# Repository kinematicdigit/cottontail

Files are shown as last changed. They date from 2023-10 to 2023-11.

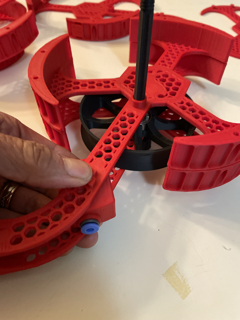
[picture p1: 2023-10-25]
IMG/IMG_6659 Small.png

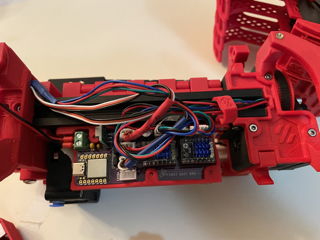
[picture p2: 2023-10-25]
IMG/IMG_6661 Small.png

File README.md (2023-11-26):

##Cotton Tail for ERCF

## BETA IS CURRENTLY CLOSED UNTIL RELEASE - TBA!

**This is project is still underdevelopment, **please proceed with caution. I hold no responsibilities for any personal damages for the use of any of these files. Please do not modifiy or share any of the files.

Any bugs, observations, questions related to this buffer can be directed at my home server at <https://discord.gg/Gs2vAtK7T7>

@kinematicdigit



Cotton Tail buffer system will attach directly to the Sturdy Bunny upgraded ERCF and is designed to work with any number of filament blocks you choose (the initial test phase will go up to 9). 

The primary goal of this project was to reduce as much resistance in the path and to remove any inconsistencies in calibration. It works with Triple Decky but will work with whatever top hat/filament block design you want. In fact, there is no limitation to the design, and it also may remove the need for magnets in them altogether. There is a spring in the couplers to alleviate all pressure on the magnets.

This system is also designed to reduce the buffer length, which will help reduce friction on the entire system. There will also be optional QoL features to work with the new BTT MMB Can board.
Features:
- Large central buffer wheel - reduces the filament's natural shape - each wheel comes pre-notched to make loading filament easier.
- Inline connection - connects to the 2020 extrusion arm
- Short Buffer Length - Can operate as low as 500mm in buffer Length
- Reduced resistance - Tests up to 200 mm/s (with Galileo 2 extruder) - may do less or more depending on your extruder motor
- Improved encoder accuracy - makes all resistance more consistent for better encoder performance and less torque needed
- Stackable Arm - Each arm is stackable for whatever combination of gates you want. They are optimized for strength and weight and provide access for loading and unloading filament
- Uses most parts from ERCP -  if you already have a kit, most parts should be interchangeable.
- Filament Detector - Each coupler has a filament detector built in. This is optional and will interface with the new BTT MMB Can board. 
- Filament indicator - Future QoL option that will include the ability to light up each gate to tell you if it is loaded/active and empty/out of filament.

###

***

### BOM (Each arm group/channel):

* (8) 8mm M3 screws
* (1) 16mm M3 screw
* (1) 25mm M3 screw
* (1) M3 threaded inserts (M3x5x4mm) Heat Sets
* PTFE Tubing (4mm OD/3MM ID recommended)
* (1) 608 ZZ Bearing (same as ERCP - skateboard bearings will work as well)
* (1) ECAS
* (2) M3 Hammerhead T-Nuts (for attaching to 2020 extrusions)

### End cap (with integrated MMB CASE) needs:

* (6) 8mm M3 screws
* (5) 25mm M3 screw (1) for non MMB
* (4) M3 threaded inserts (M3x5x4mm) Heat Sets (0) for non MMB

**The optional MMB version build requires:**

(1) BTT MMB Can board
(1) Microswitch per arm
(1) 5.5 mm ball bearing per arm
(2) 12mm M2 BHCS screws per arm
(1) Button Neopixels per arm

***

## Building the ERCT

All files are located in the STL folder, and instructions are as follows:

|  |
| :-----------------------------------------------------------------------------------------------------------------------------------------------------------------------------------------------------------------------------------------------------------------------------------: |
|                                                                                            Each channel uses these parts. ERCT is all stackable with a single endcap to finish the buffer.                                                                                            |

### **Instructions**

**PRINT SETTINGS**

.25mm first layer, .2mm Layer Height
4 Perimeters (top, bottom, walls

Arms should be printed at .2 layer height, with 4 walls and 10% lightning infill. This will significantly reduce the amount of filament used. ABS is the recommended material or PETG.

Wheels should be printed on a smooth plate, or if you use a textured plate you may need to run it on some sandpaper afterwards to avoid too much contact with the arm. There will always be a small chance of some rubbing, but with careful pressure on the hubs when installing, you shouldn't have any major resistance.

The rest of the parts can be printed with 20-30% gyroid infill.

|   | Start with your printed channel arm and add a 4 mm-deep M3 heatset installed into the back of the arm. Be careful not to go too far past the dovetail channel- it's better to be shy than to go over. |
| ---: | --- |
|   | Print the correct length axial screw. The files are labelled for how many channels. They are longer than needed in case you need to put a bypass divider or extra support. Use the matching nut and work it through the acme screw to make it smooth. A brass brush can also be used to clean it up a little. It is recommended if you make more than 9 channels, to self-source a trapezoidal bar screw (also known as ACME screw). T8, Pitch 2 is a common one. You can also use a traditional screw. Make sure to get matching nuts to add to each end for those builds. |
|   | Load the axial through the first arm. |
|  | The 608 bearings should slide in with just a tiny bit of resistance. |
|   | Make sure the filament loading holes are as pictured, and load the axial from the flat side of the wheel. |
|   | When pushing down on the axial, put your thumbs on each side of the bearing and push down with moderate force. Don't push too hard. If it doesn't go on, use a little sandpaper on the axial to reduce it. It is a tight fit but should slide on. Your pressure on the bearings will ensure the wheel is as balanced as possible. There's a very tiny bit of gap between the wheel and the side of the arm. Don't worry too much if it isn't perfect, but you can try to balance it and spin it to check. |
|  | Preload the M3 Hammerhead T-Nuts onto the mounting bracket. Don't screw in too tight as you need to turn the nuts easily to load into the v-slots of the 2020 extrusion. |
|  | Load the mount onto the arm. The dovetail is snug but should slide on with some pressure. Once seated add the M3 16mm screw to secure it. |
|  | Squeeze the printed spring (the spring goes towards the ECAS side) and slide into the slot on the sloped side.&#xA; |
|  | Add ECAS fitting in the hole. It should snap-in and firm press.&#xA; |
|  | line up the coupler as pictured to the three receiving pins. It should press fit with a small bit of resistance. Repeat the next channel arm until all is loaded. |
|  | When you reach the final channel, you will add the end cap and install the final M3 25mm screw. |
|  | Secure all 6 screws, which enter at an angle. They self-tap into the plastic, so don't over-tighten or you'll strip the plastic. These install and reinstall multiple times if you don't over-tighten.  &#xA; |
|  | The next step is prepping the ERCF. If you have wiring clips, remove them and free all your wires. |
|  | Line up the t-nuts as best you can. Make sure you didn't wind them all the way down. The screws should have enough friction to hold them in place to make this part easier for you. It should sit right on the shoulder and slip in. If not, jiggle the arms a little; it should all mate perfectly. Grab your driver and turn, and it should tighten right away. If not, back off a quick half-turn and turn the back the other way to load the nut in place. |
|   | The last set of steps starts by cutting around 85mm of tube which should leave around 10mm of tube sticking out of the coupler block. |
|  | Insert the cut PTFE tube from the rear of the assembly. Push lightly in the spring, and it should feed through. |
|  | Line up to the channel and press into the ECAS on the filament block. |
|  | The rest of the tube can be trimmed to around 10mm. |
|  | The wires can now be routed against the mounting brackets and you can use zip ties to secure it. |

***

**LOADING THE BUFFER**

|  | To load the buffer, filament from your reverse Bowden. Try your best to work with the natural curl of the filament and feed it till you see it pop out on top. |
| ---: | :--- |
|  | Grab it from up top, and curl it back into one of the multiple filament loading holes located along one side of the buffer wheel. |
|  | Turn the wheel until you have the number of rows needed for your tube length between the ERCF encoder and the tool head (to calculate the right length, measure the tube and divide by 230mm. This will equal the number of rows you need to wrap around the wheel - maximum of 7). |
|  | Back below, grab the filament on the wheel and pull it out. |
|  | Give yourself some length (about 30 cm). |
|  | Feed back into the tube located there. |
|  | It will feed through, and you should feel some resistance from the trap; press on the top hat to help it through. |
|  | The final step is to push the filament flush to the opening so it doesn’t catch on the selector. That’s it. Load it all up, and away you go! |

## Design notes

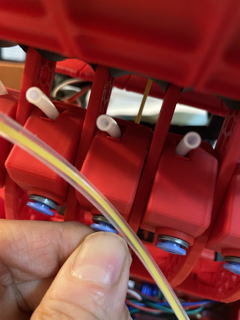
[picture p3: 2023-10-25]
IMG/IMG_6672 Small.png

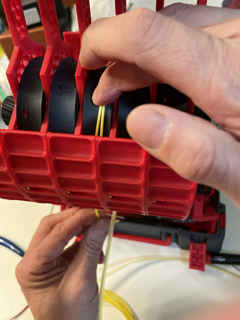
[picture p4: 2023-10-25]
IMG/IMG_6676 Small.png

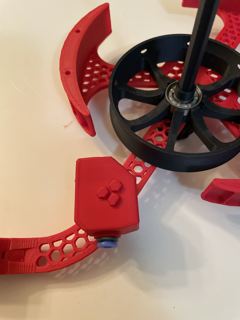
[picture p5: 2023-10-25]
IMG/IMG_6658 Small.png

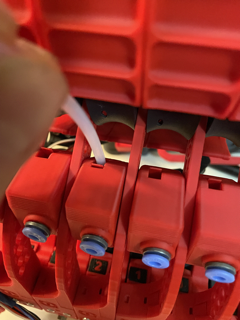
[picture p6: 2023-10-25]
IMG/IMG_6666 Small.png

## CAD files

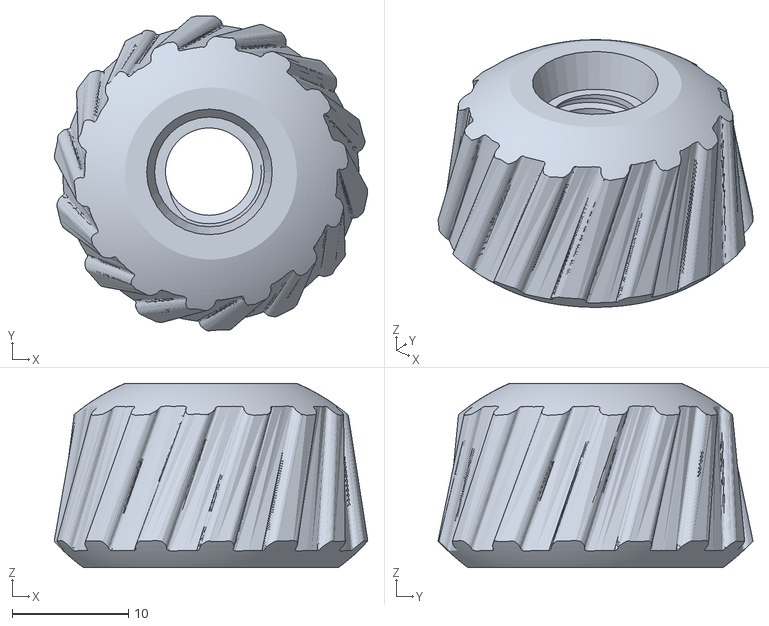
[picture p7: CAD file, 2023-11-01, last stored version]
STLS/[a]knut.stl
27.0 x 27.1 x 15.9

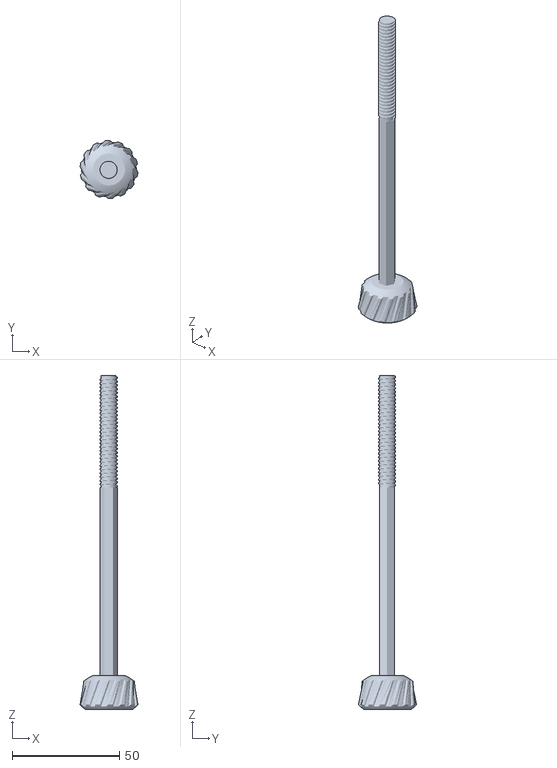
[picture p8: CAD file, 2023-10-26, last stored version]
STLS/axials/[a]kaxial_5.stl
27.0 x 27.1 x 155.6

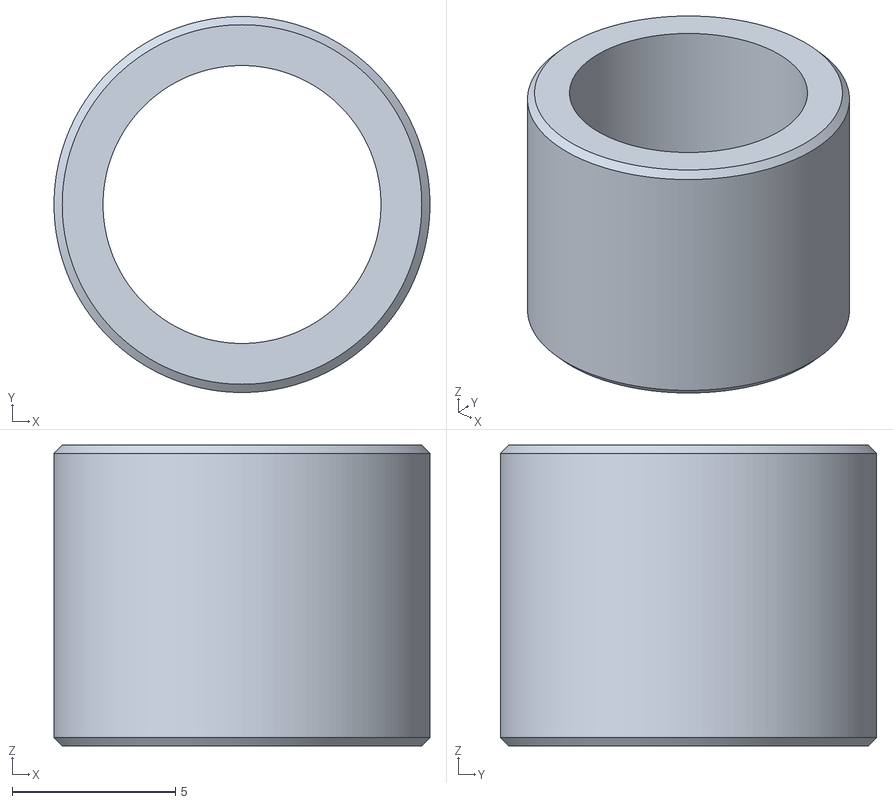
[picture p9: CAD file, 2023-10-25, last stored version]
STLS/buffer_wheel/spacer_bypass.stl
11.5 x 11.5 x 9.20

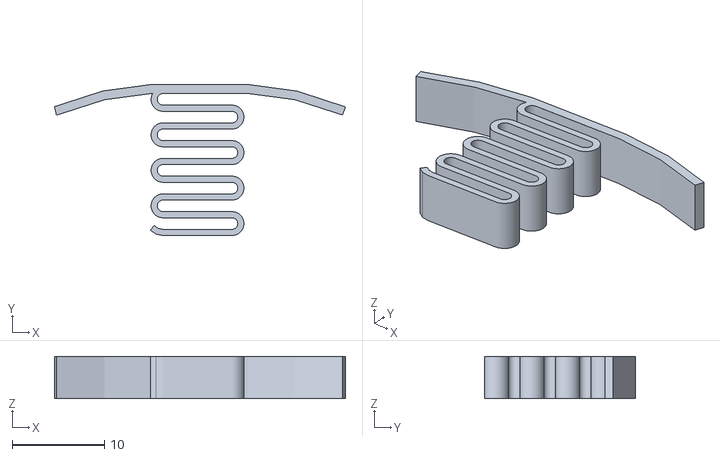
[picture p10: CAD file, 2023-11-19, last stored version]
STLS/coupler/coupler_spring.stl
31.6 x 16.4 x 4.59

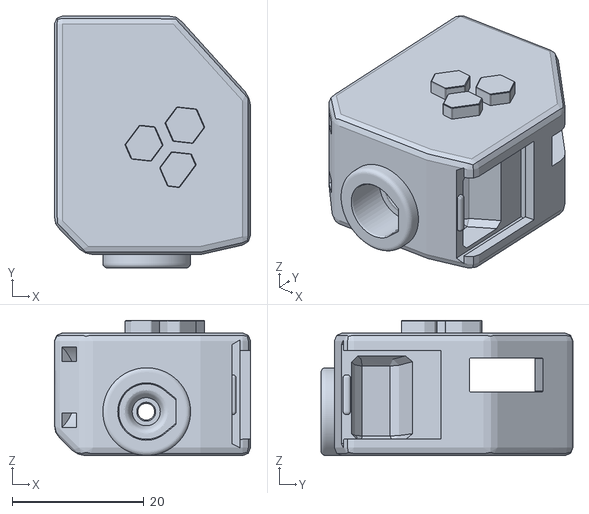
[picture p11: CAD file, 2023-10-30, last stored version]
STLS/coupler/MMB_option/[t]coupler_block_MMB.stl
29.7 x 38.2 x 20.5

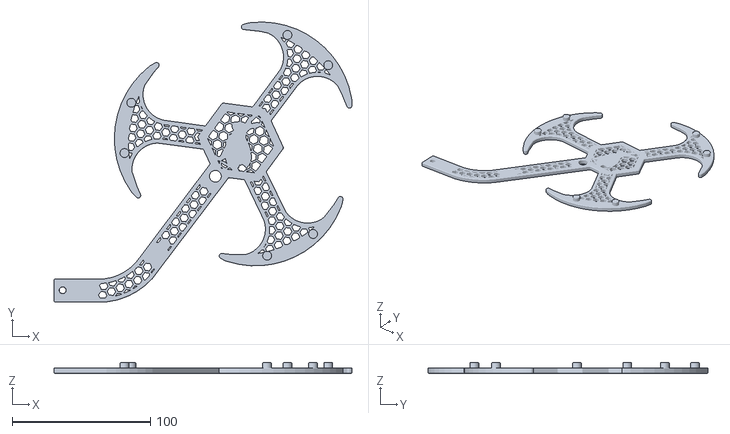
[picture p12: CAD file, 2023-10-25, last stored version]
STLS/support_arms/support_arm_endcap.stl
215.7 x 202.6 x 7.67

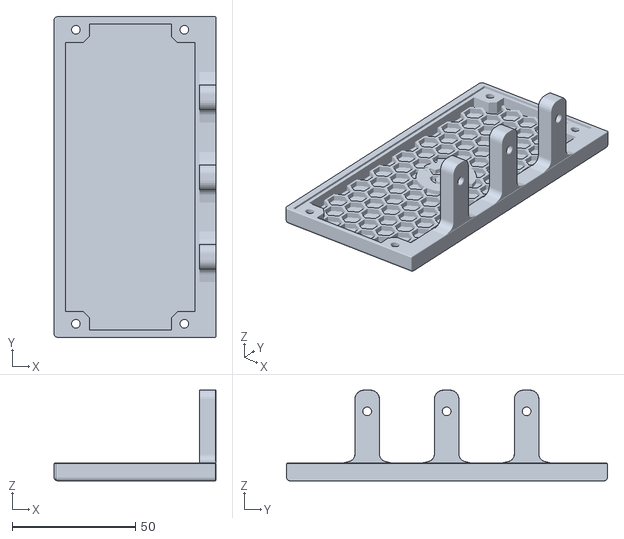
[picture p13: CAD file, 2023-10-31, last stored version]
STLS/supports/BTT_MMB/[a]BTT_MMB_Bottom_Bracket.stl
65.6 x 130.0 x 36.8

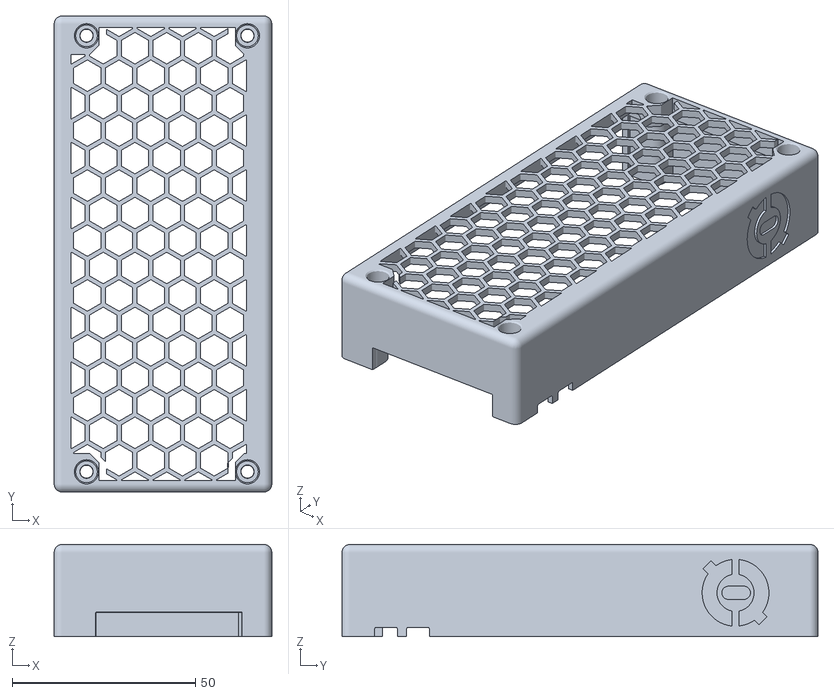
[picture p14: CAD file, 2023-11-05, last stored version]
STLS/supports/BTT_MMB/bottommount/[a]BTT_MMB_Top_Lid_Standard.stl
59.4 x 130.0 x 25.1

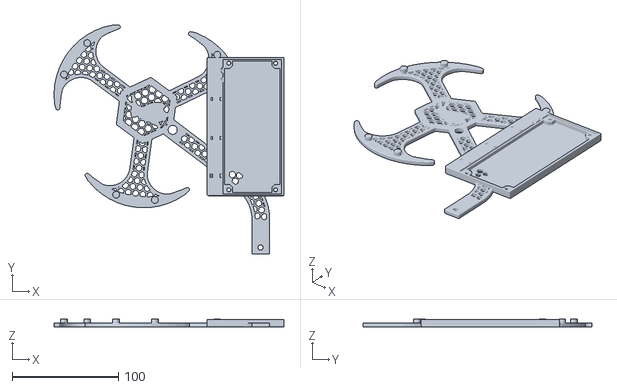
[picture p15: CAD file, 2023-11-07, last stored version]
STLS/supports/BTT_MMB/buffermount_recommended/[a]BTT_MMB_Bottom_Bracket_universal.stl
216.2 x 215.7 x 7.67

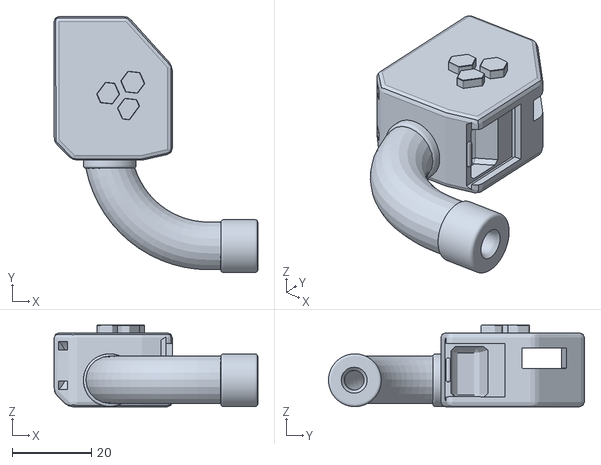
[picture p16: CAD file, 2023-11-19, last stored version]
STLS/testing_experimental/coupler_block_180.stl
51.3 x 64.4 x 20.5

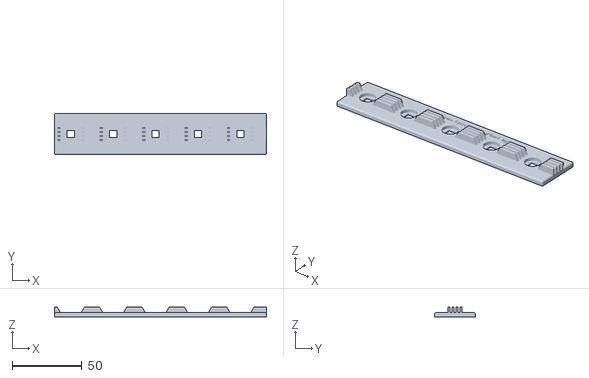
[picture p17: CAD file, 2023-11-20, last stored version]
STLS/tools/LED_Soldering_tool_holder_by_jose.stl
152.5 x 29.5 x 7.00

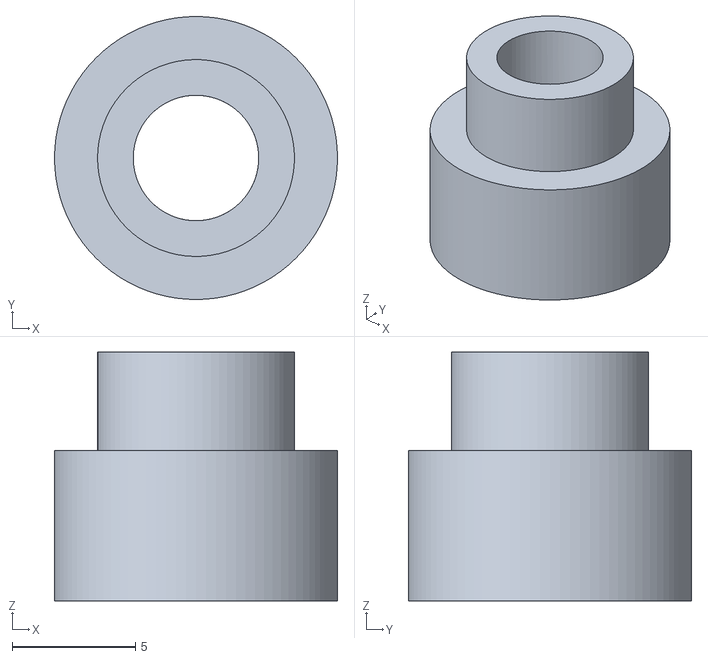
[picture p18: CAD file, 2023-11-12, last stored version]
usermod/Wolffy01/625 mod w 5mm tread rod/stl/5mm arm end cap bushing.stl
11.5 x 11.5 x 10.1

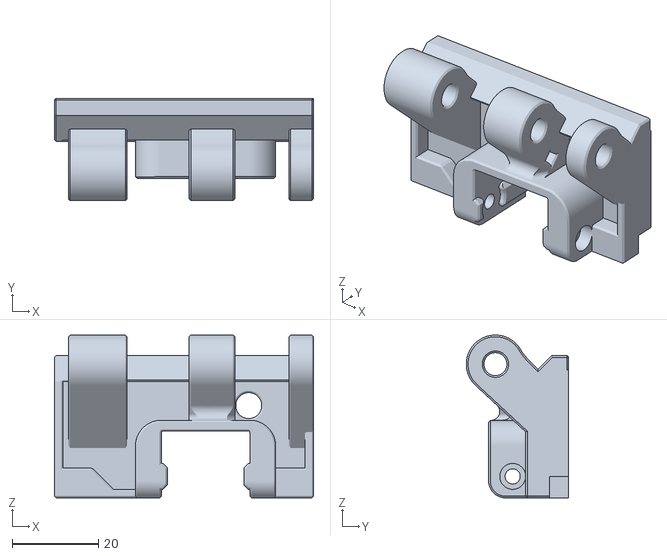
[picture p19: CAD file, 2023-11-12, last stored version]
usermod/Wolffy01/filament_block_end/Filament_Blocks_End_Nobearing_V2C.stl
60.0 x 23.7 x 37.7

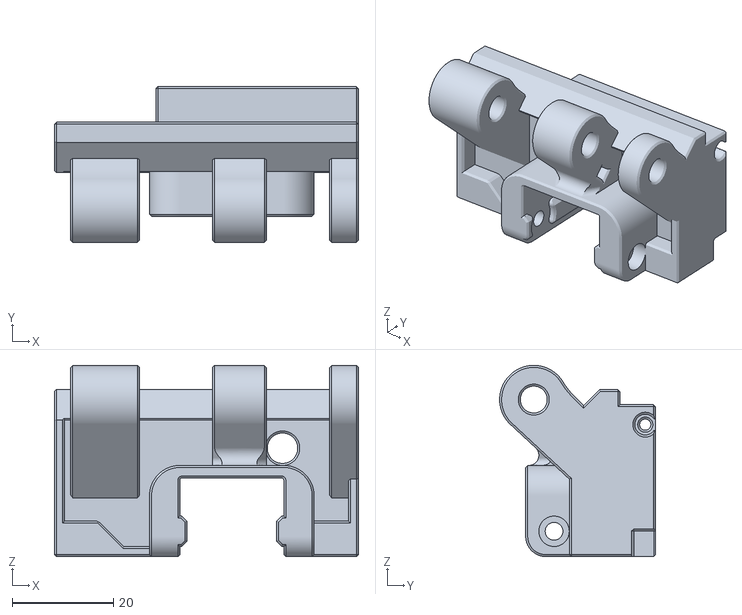
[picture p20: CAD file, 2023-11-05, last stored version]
usermod/wolffy01_filament_block_end/Filament_Blocks_End_Nobearing_V2B.stl
60.0 x 30.8 x 37.7

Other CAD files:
STLS/buffer_wheel/spacer_standard.stl
STLS/coupler/MMB_option/[black]LED_carrier.stl
STLS/axials/[a]axial_spacer.stl
STLS/axials/[a]kaxial_6.stl
STLS/axials/[a]kaxial_7.stl
STLS/axials/[a]kaxial_8.stl
STLS/axials/[a]kaxial_9.stl
STLS/axials/[a]knut.stl
STLS/buffer_wheel/[a]buffer_wheel.stl
STLS/coupler/LED_carrier.stl
STLS/coupler/[a]coupler_block_standard.stl
STLS/coupler/[b]coupler_spring.stl
STLS/coupler/[b]coupler_spring_thicker.stl
STLS/coupler/[black]LED_carrier.stl
STLS/coupler/coupler_spring_thicker.stl
STLS/support_arms/[a]support_arm_mount.stl
STLS/supports/BTT_MMB/bottommount/[a]BTT_MMB_Bottom_Bracket.stl
STLS/supports/BTT_MMB/bottommount/[a]BTT_MMB_Top_Lid_180.stl
STLS/supports/BTT_MMB/buffermount_recommended/[a]support_arm_endcap_case.stl
STLS/supports/BTT_MMB/buffermount_recommended/support_arm_endcap_case.stl
STLS/testing_experimental/[a]arm_anchor_ptfe.stl
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

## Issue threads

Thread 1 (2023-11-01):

soldering tool orientation

99dreada, 2023-11-01:
soldering tool orientation by default is not in a printable way

easy fix but would be nice to be done by default

99dreada, 2023-11-01:
to add to this the Knut is also upside down

kinematicdigit, 2023-11-01:
Thanks for that... reoriented.

Closed 2023-11-01.

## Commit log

2023-10-25 Initial commit
    Update [a]support_arm_mount.stl
    bevelled tip of dovetail
    Adjust Tolerances
    October 23 Late update
    Add files via upload
    Create .gitignore
    Update Oct 23
    New Uploads
    New Uploads
    Create support_arm_00.stl
    [LED_Soldering_tool_holder.stl, LED_carrier.stl, [a]axial_spacer.stl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]
2023-10-25 renaming and reorganizng
    [[a]axial_spacer_bypass.stl, spacer_standard.stl]
2023-10-26 No number plate arm.
2023-10-26 Replace Corrupted File
    [[a]kaxial_5.stl]
2023-10-27 number plate holder update
    Use the same plates found in the Triple Decky repo
2023-10-27 renamed, blank and number plate holder
2023-10-28 Thicker spring for slicers that are having issues with 6mm ones.
    Optional thicker version. This is strictly for slicers that are having issues with the .6mm thick spring. This one is .7mm thick.
    [[b]coupler_spring_thicker.stl]
2023-10-28 ECAS update - now snap fit instead of just a press fit.
    Updated coupler to be snap in fit instead of just a pressure fit. Utilizes a 8.6mm step inside to hold the coupler in place better. Old version will work, but this just makes it a little more secure.
    Thanks to @danzaywer for bringing this to my attention.
    [[a]coupler_block_standard.stl, [t]coupler_block_MMB.stl]
2023-10-30 Coupler Block for BTT MBB versions
    Updated filament path and optimized micro switch operations.
    [[t]coupler_block_MMB.stl]
2023-10-31 BTT_MMB Bracket
    for 2020 extrusion (ERCF - Sturdy Bunny)
    [[a]BTT_MMB_Bottom_Bracket.stl]
2023-11-01 Reoriented for optimal print positions
    [[a]knut.stl]
2023-11-05 Case updates got BTT MBB
    Several Case options for the BTT MBB for use with Cotton Tail.
    The recommended case is on the buffer, but if you want to bottom mount onto the ERCF, I recommend you have at least an 8 channel version minimum for the optimal wire clearance.
    [Filament_Blocks_End_Nobearing_V2B.stl, [a]BTT_MMB_Bottom_Bracket.stl, [a]BTT_MMB_Bottom_Bracket_universal.stl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]
2023-11-06 Fixed a shift in the model.
    [[a]support_arm_endcap_case.stl]
2023-11-06 bug fix
    [[a]BTT_MMB_Bottom_Bracket_universal.stl, [a]support_arm_endcap_case.stl]
2023-11-06 Adjust clearance for EZ drivers.
    [[a]support_arm_endcap_case.stl]
2023-11-07 Alignment error corrected
    [[a]BTT_MMB_Bottom_Bracket_universal.stl]
2023-11-12 testing folder added, and some renaming
    This update includes a new testing folder, and the LED carrier has been renamed
    [[a]buffer_wheel_V6_0.4mm_0.15offset.stl, [a]knut_T8_p2.stl, [black]LED_carrier.stl]
2023-11-12 Test folder, renaming, and usermods added.
    This update includes a new testing folder, the LED carrier has been renamed, and mods from Wolffy01 for a 625 bearing adapter (to use the original rod from ERCF) and for a filament bearing block end 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
    [5mm arm bushing.stl, 5mm arm end cap bushing.stl, 625 case end cap.stl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]
2023-11-13 update knut tolerance
    [[a]knut_T8_p2.stl, [a]knut_T8_p2_tolerance+1.0.stl, [a]knut_T8_p2_tolerance+1.5.stl]
2023-11-13 Reorganizing files
    [[black]LED_carrier.stl, [t]coupler_block_MMB.stl]
2023-11-17 plate orientation
    [[a]knut_T8_p2_tolerance+1.0.stl, [a]knut_T8_p2_tolerance+1.5.stl]
2023-11-19 New experimental parts
    New experimental parts to try:
    Anchors for right angle 180 degree coupler - [a]arm_anchor_ptfe
    right angle coupler block - coupler_block_180
    4 degree outlet coupler block - coupler_block_angled
    new updated/replacement spring that shouldn't error on various slicers now.
    [[a]arm_anchor_ptfe.stl, coupler_block_180.stl, coupler_block_angled.stl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]
2023-11-20 New LED Tool by Jose
    LED jig tool for the MMB version of the coupler block
    [LED_Soldering_tool_holder.stl, LED_Soldering_tool_holder_by_jose.stl]
2023-11-26 Beta Closed
    [5mm arm bushing.stl, 5mm arm end cap bushing.stl, 625 case end cap.stl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]
